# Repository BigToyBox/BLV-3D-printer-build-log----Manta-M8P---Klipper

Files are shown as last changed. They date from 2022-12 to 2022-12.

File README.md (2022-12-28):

# "The WASP" - a BLV CoreXY printer build with MantaM8P and Klipper

#### This is a log of my BLV mgn cube 3d Printer. I built the the FYSETC kit with Bluerolls metal kit recommended by Ben Levi. 

This guide combines the build guides and metal kit animations from Ben Levi, FYSETC factory videos, and David Husolo's guide on [ifixit](https://www.ifixit.com/Device/BLV_MGN_Cube) to provide a build flow that I followed to assemble my BLV printer. It's not the ONLY way to accomplish the build, it's simply a log of how I worked my way thru the build. 

### Modifications include:
- BTT Manta M8P with their CB1 pi clone
- Klipper firmware
- BIQU H2 direct drive extruder mounted with the BIQU hermit crab back plate
- Induction probe for z sensing (I run the same probe on teh Manta, an Octopus and a SKR2)
- My own neopixel code controlled directly by the MantaM8P (no daughter board required)
- Microsoft camera 
- Noctua quiet power supply fan per David's guide on ifixit
- Magnetic print bed with spring steel PEI build plate
- Left and right LED light buttons (shutting off the side oppsite the camera improves video quality 
- Tool tray for tweazers and cutters
- Dual filament spool holders





## My build includes the following mods:

3. Neopixels controlled by the Manta board

## STL files
1. Bigtreetech H2 extruder/hermit crab mount adapted to the metal kit (ADXL345 mounting holes included)
2. Adapter mount plate from the Duet mounting holes to the Manta M8P board with triple fans
3. TPU mounting feet
4. Redesigned LED light strip diffusers
5. Redesigned LED neopixel diffusers
6. 

## Manta M8P-CB1 firmware
** Firmware available on request

## Configuration Checks

From the Voron website:
Stepper motor direction setup (voron site)

## Step 1 - Endstop tests
* Test each endstop by using the "Endstop" tab within the "Machine" page
* Adjust logic as needed by doing research online and/or with your board
    For the Manta M8P ..............TBD

## Step 2 - Motor tests
* Be sure to be ready to manually trip the endstop(s) with your finger if the motor(s) are moving in the wrong direction

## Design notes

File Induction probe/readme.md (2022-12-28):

# Induction probe installation

## Two for $11.99

induction probe

Installing an induction probe is not complicated compared to the BL Touch. The reason so many people struggle and fail is because they think the probe is supposed to be powered with 5 volts to provide the required 5 volt output. It needs to be powered at the highest DC voltage you have available on your board. It works with 12 volts but 24 volts is best. I simply use a spare fan port and set the pin to the highest available. 

#### Sample code:

[probe]
pin: !PF6 # set for the pin of YOUR board!

x_offset: 35 # this is the offset for my probe mount to a H2 extruder

y_offset: -28 # this is the offset for my probe mount to a H2 extruder

speed: 20

samples: 2

samples_result: median

#### * Go to the klipper endstop test menu and test the logic using a metal object (I use a metal ruler)
#### ** When testing the probe, have a metal ruler handy. Manually run your gantry up far from the bed try a z home and immediately use your metal ruler to test the probe. If it doesn't stop the gantry, you have time to hit the panic button!

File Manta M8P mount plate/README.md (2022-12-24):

## Manta M8P Mount Plate
I created a mounting plate to mount my Manta M8P in the existing Duet mounting holes. I used the three extra fans that came with the Fysetc kit and put them to good use cooling the stepper drivers.

1. Print in PLA or PETG

2. Connect to "Motor fan" port as shown in the picture. There is no configuration necessary. This fan port runs when the board is powered up. 



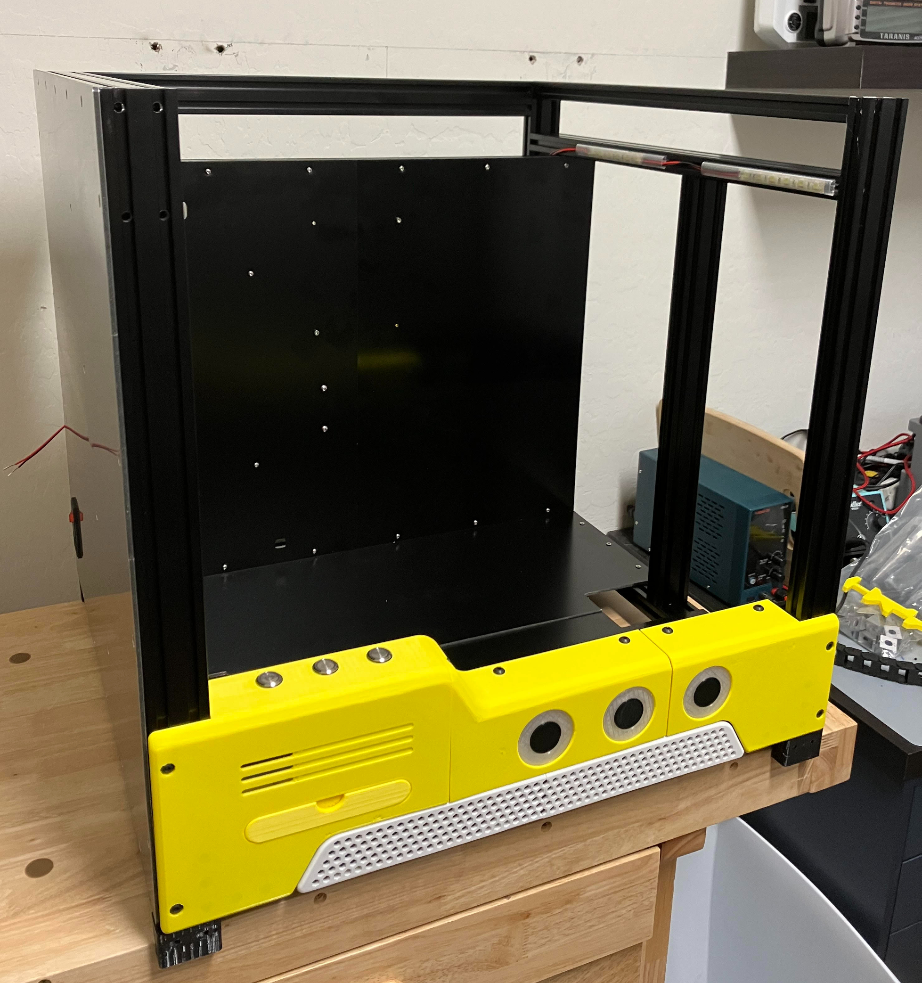
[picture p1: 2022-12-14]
blv2.jpg

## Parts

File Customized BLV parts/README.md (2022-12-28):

# Customized BLV parts

To better segment the neopixel light rings, I modified the lenses and backplates. Choose an insert, drop in the neopixel ring and attach the back plate to sandwich it all together. There are small alignment marks to help you line up the leds square in the lens. 

## Custom neopixel parts and code

https://user-images.githubusercontent.com/120577343/209478114-9a8a7863-4ae0-4498-9a60-9b79ae05963c.MOV

https://user-images.githubusercontent.com/120577343/209478135-262ede98-7630-4743-8846-90822e58087a.MOV 

https://user-images.githubusercontent.com/120577343/209478141-fe76ba48-79a5-4c61-93c1-53a307766526.MOV

lens inserts

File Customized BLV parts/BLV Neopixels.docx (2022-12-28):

Neopixel basic colors:

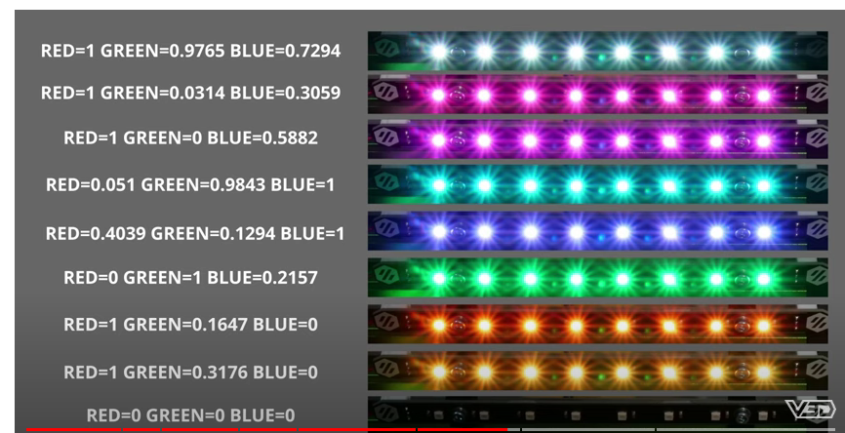
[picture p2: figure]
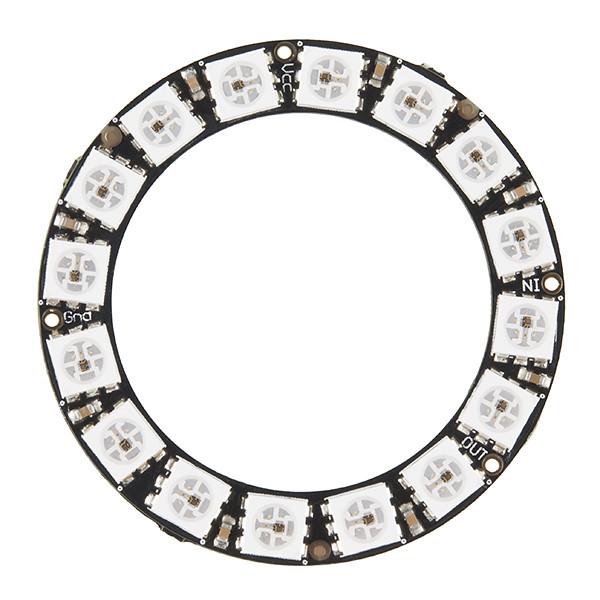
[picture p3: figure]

LEFT CENTER RIGHT

SCHEME:

Power up Manta M8P wiring

Green left ring lower and upper IN VCC GND PIN# .

Green first led center ring Left/Center Pink Red Brown PC6

Light red right ring Right Yellow Green Blue PA9

Bed heat - lower left ring

Yellow progress sequence during warm up

Red when at temp

Extruder heat - upper left ring

Yellow progress sequence during warm up

Red when at temp

Print progress - center ring

Blue progress sequence

Failure - right ring

Red flashing for errors

Red while extruder and bed are above 50C warning against a power shutdown

1. Install:

cd ~

git clone https://github.com/julianschill/klipper-led_effect.git

cd klipper-led_effect

./install-led_effect.sh

2. Add to printer.cfg

[include led_configuration.cfg]

[neopixel left]

pin: PC6

chain_count: 32

initial_red: 0

initial_green: 0

initial_blue: 0

[neopixel right]

pin: PA9

chain_count: 16

initial_red: 0

initial_green: 0.2

initial_blue: 0.2

3. Create led_configuration.cfg:

[led_effect panel_idle]

autostart: true

frame_rate: 24

leds:

neopixel:left (4,5,12,13)

layers:

breathing 10 0 top (.1,.2,0)

[led_effect power_idle]

autostart: true

frame_rate: 24

leds:

neopixel:right (1,3,5,7,9,11,13,15)

layers:

breathing 10 0 top (0.2,0.05,0.0)

[led_effect progress_idle]

autostart: true

frame_rate: 24

leds:

neopixel:left (17,32)

layers:

breathing 10 0 top (0.01,.01,.03)

[led_effect bed_effects]

leds:

neopixel:left (1-8)

neopixel:right (2,4,6,8,10,12,14,16)

autostart: true

frame_rate: 24

heater: heater_bed

layers:

heater 50 0 add (.1,0,0)

[led_effect extruder]

leds:

neopixel:left (9-16)

neopixel:right (2,4,6,8,10,12,14,16)

autostart: true

frame_rate: 24

heater: extruder

layers:

heater 50 0 add (.1,0,0)

[led_effect progress_bar]

leds:

neopixel:left (18-32)

autostart: true

frame_rate: 24

layers:

progress -1 0 add ( 0, 0, .1),( 0, 0.1, 0.6)

[led_effect critical_error]

leds:

neopixel:right (2,4,6,8,10,12,14,16)

layers:

strobe 1 1.5 add (1.0, 1.0, 1.0)

breathing 2 0 difference (0.95, 0.0, 0.0)

autostart: false

frame_rate: 24

run_on_error: true

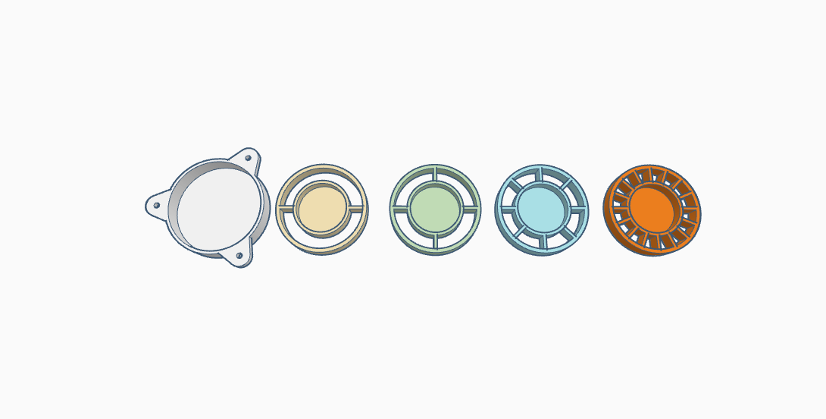
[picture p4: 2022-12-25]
Customized BLV parts/lens inserts.png

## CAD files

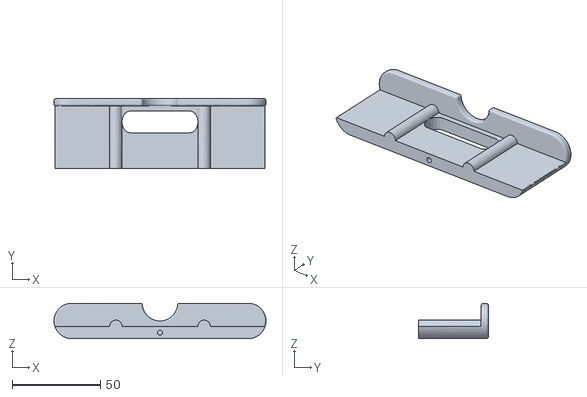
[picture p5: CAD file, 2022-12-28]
Customized BLV parts/Front pull out tool tray.stl
120.0 x 39.4 x 20.0

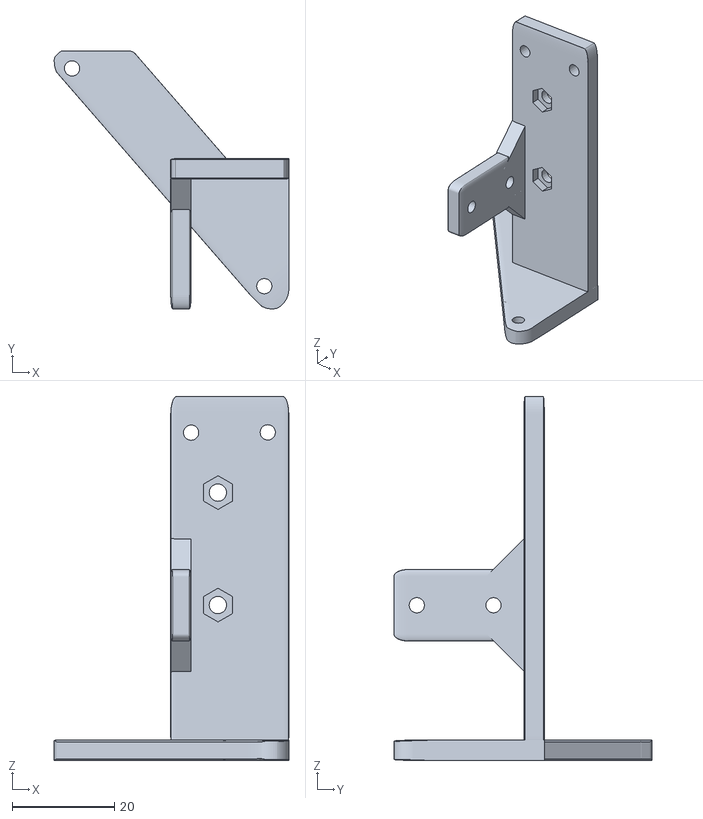
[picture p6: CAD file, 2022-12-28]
H2 - Hermit crab setup/H2 upper mount.stl
45.9 x 50.5 x 71.2

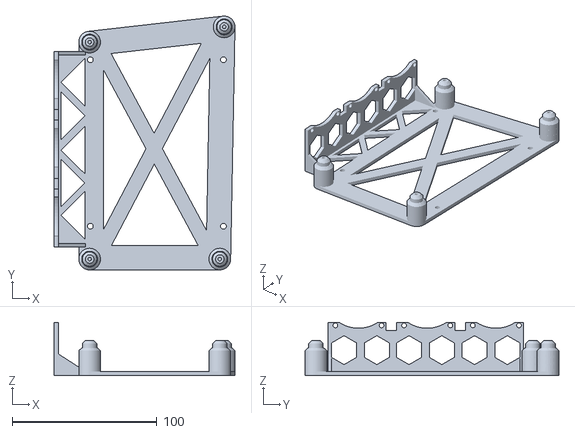
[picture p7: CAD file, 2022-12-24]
Manta M8P mount plate/Manta M8P mount.stl
125.1 x 175.5 x 36.9

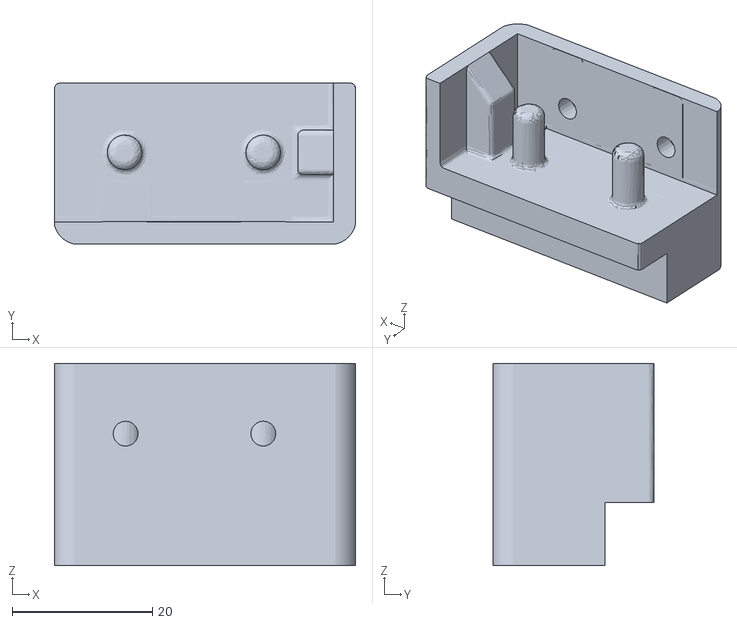
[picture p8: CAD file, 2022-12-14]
Mounting feet/BLV locking foot.stl
43.0 x 23.0 x 28.9

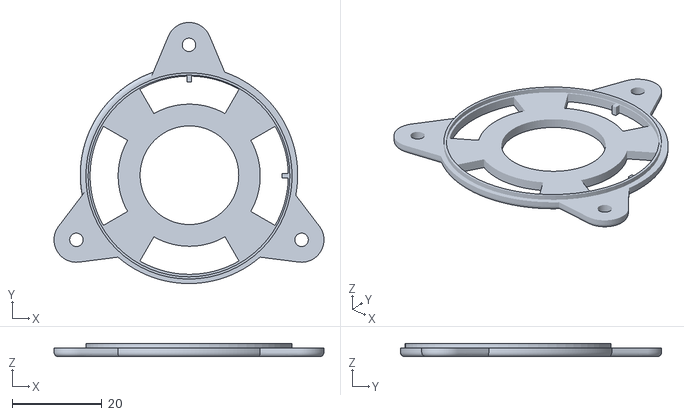
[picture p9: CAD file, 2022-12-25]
Customized BLV parts/neopixel lens back plate.stl
60.2 x 58.2 x 3.00

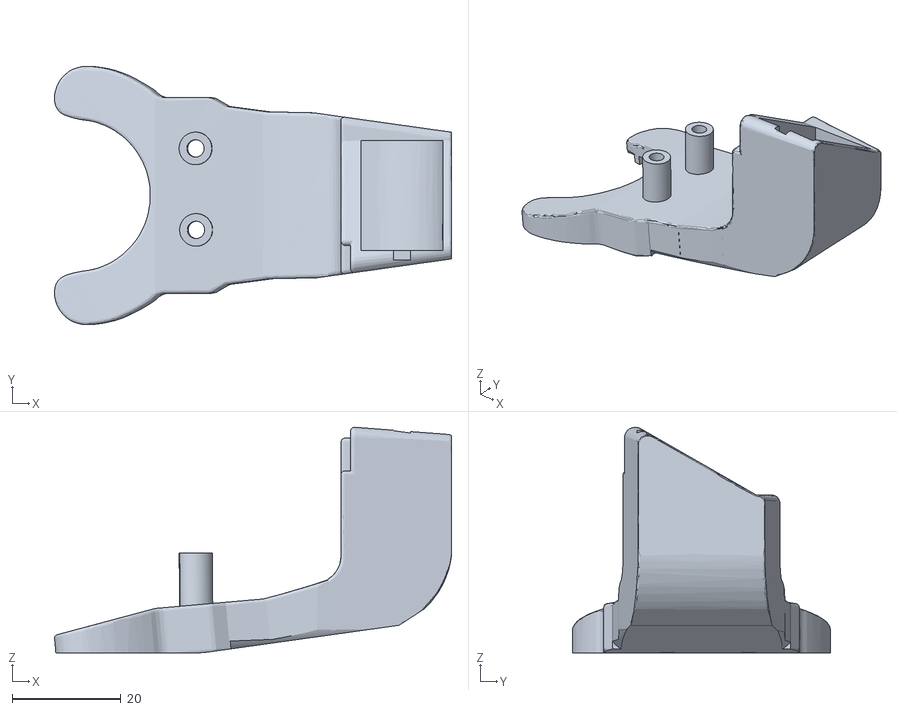
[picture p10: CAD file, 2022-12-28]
H2 - Hermit crab setup/H2 extruder fan duct.stl
73.1 x 47.6 x 41.5

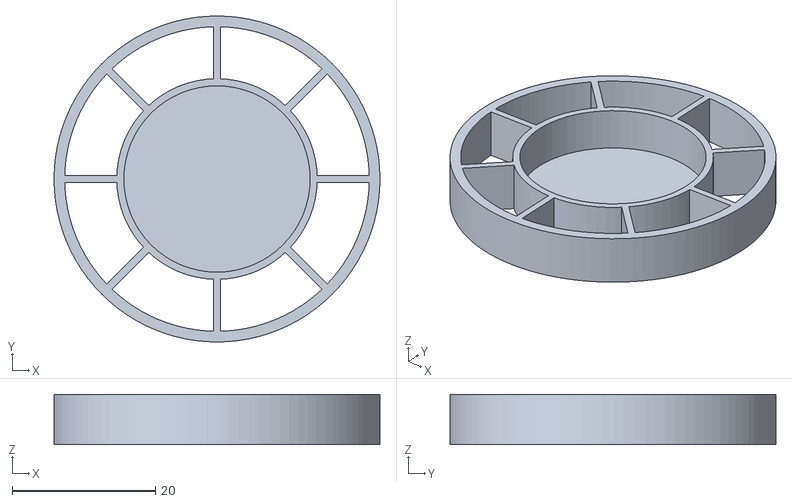
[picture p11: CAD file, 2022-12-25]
Customized BLV parts/neopixel 8 segment face.stl
45.5 x 45.5 x 7.00

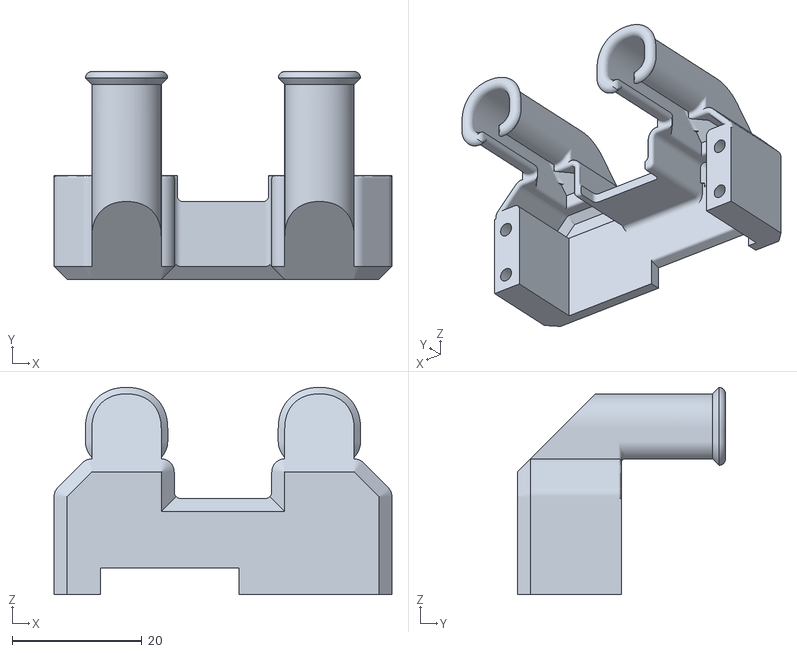
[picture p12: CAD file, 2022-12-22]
H2 - Hermit crab setup/Hermit Crab Cap.stl
52.0 x 32.0 x 31.9

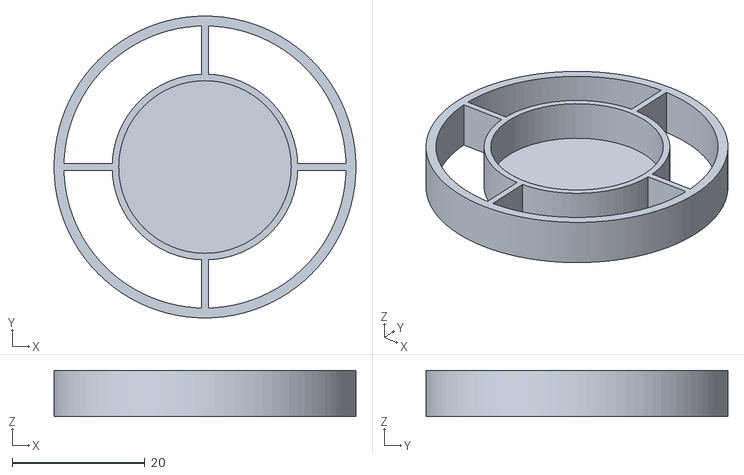
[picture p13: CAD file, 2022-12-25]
Customized BLV parts/neopixel 4 segment face.stl
45.5 x 45.5 x 7.00

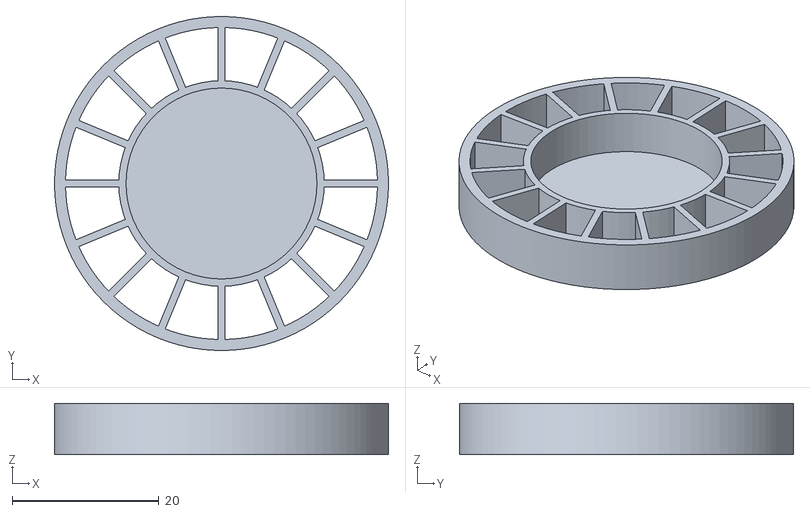
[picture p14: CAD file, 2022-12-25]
Customized BLV parts/neopixel 16 segment face.stl
45.5 x 45.5 x 7.00

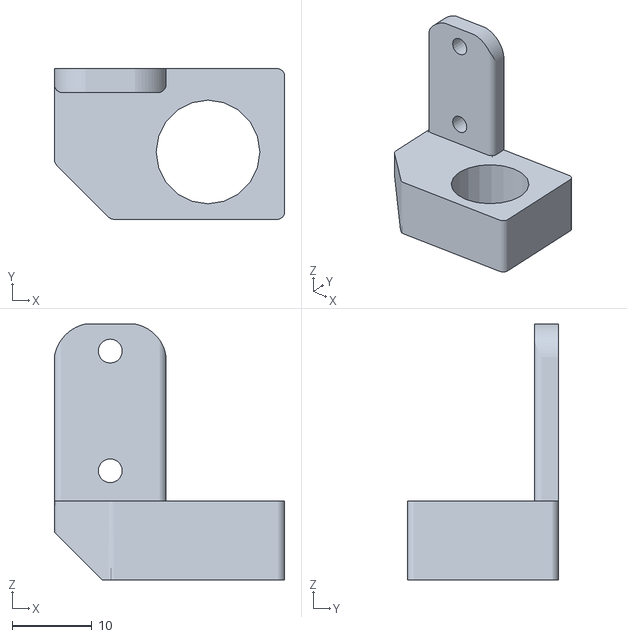
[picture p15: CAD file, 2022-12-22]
H2 - Hermit crab setup/H2 probe mount.stl
28.9 x 18.9 x 32.1

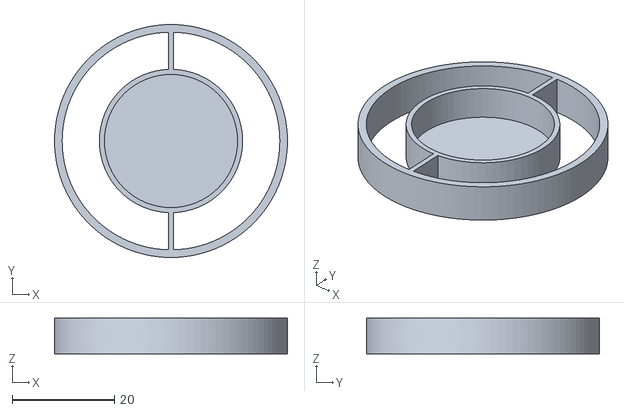
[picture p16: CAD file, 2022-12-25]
Customized BLV parts/neopixel 2 segment face.stl
45.5 x 45.5 x 7.00

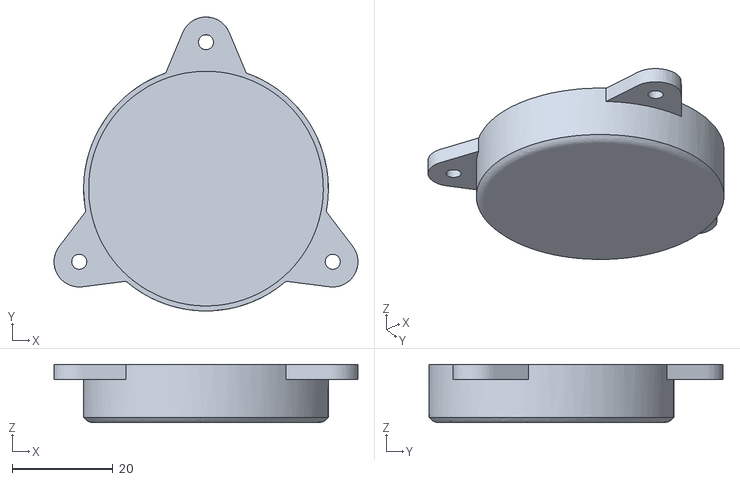
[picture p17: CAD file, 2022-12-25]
Customized BLV parts/neopixel smooth lens.stl
60.2 x 58.2 x 11.5

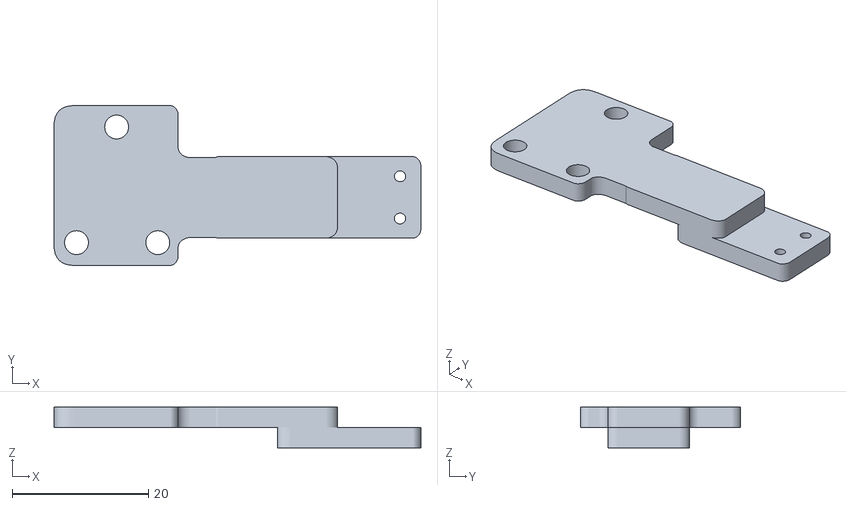
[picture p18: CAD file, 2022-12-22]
Customized BLV parts/X endstop long switch mount.stl
54.0 x 23.5 x 6.00

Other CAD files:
Customized BLV parts/Microsoft_HD_3000_2020_Rail_Mount.stl
Customized BLV parts/LED diffuser set.stl
H2 - Hermit crab setup/H2 to carriage spacer nut plate.stl

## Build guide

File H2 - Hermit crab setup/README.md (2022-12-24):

## Biqu H2 extruder and Biqu Hermit crab Assembly

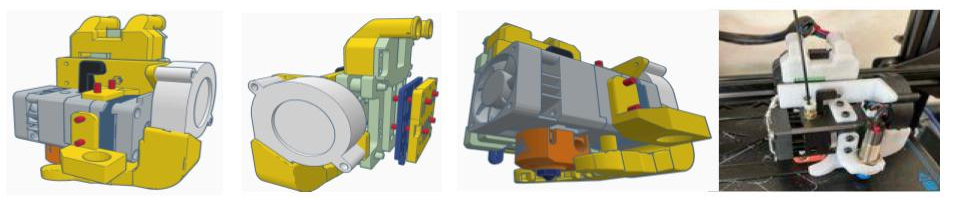
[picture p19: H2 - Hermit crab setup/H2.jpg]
H2 Hermit Crab BLV metal kit mount


## Step 1 - Print the parts:
Print the parts in PETG
 * The upper H2 mount prints best vertical as shown with a support
 * The fan duct prints flat without supports

## Step 2 - Hermit Crab back plate:
1. Insert four M3 nuts into the nut plate spacer
2. Assemble the front metal plate, the spacer and the metal top plate together OFF the gantry using two bolts provided with the metal kit
 #### You MUST USE the exact length of bolts for the top mount locations! A longer bolt will drive into the upper metal part and NOT tighten the hermit crab  plate down properly!
3. Carefully drill out the the front metal plate using the spacer as your drill guide

  

6. Finish assembly of the gantry extruder carrier
7. Bolt the back plate of the hermit crab to the face of the extruder mount using the bolts provided by BIQU
8. Connect your wires and install the wire cap

 

### Step 3 - H2 extruder assembly:
1. Remove the wiring plate from the hermit crab plate. Install the H2 with one bolt in the lower left of the plate to the lower left hole in the back of the H2 extruder. Leave it snug to allow for alignment later. 
2. Install the printed top mount using two bolts and nuts to attach it to the plate and two more bolts to attach it to the H2 extruder. Tighten the printed mount to the top of the H2 extruder first, then snug up the bolts to the plate. The printed mount si designed to provide a top "fence" for the H2 to rest against so align the H2, the printed upper mount, and the hermit crab plate so the H2 sits flush against the mount and everything is square to teh back plate. Tighten all 5 bolts. 
3. Attach the fan to the side of the mount
4. Attach the fan duct to the bottom of the H2 extruder
5. Attach the probe mount to the front of the extruder (substitute a BL touch mount if that is your preference)
6. Route all wires

  
 

## Enjoy the ease of having swappable extruders!
#### In my workflow, I have three of these assemblies, one for each printer and a fourth spare H2 assembly ready to go should one of my other H2's fail. 

#### * Note: It is impossible to have every probe set exactly the same distance from teh nozzle tip. When you swap extruders, you have to do a quick z offest "tune" using the piece of paper method. However, due to the precise design of the hermit crab system, you do NOT have to recalibrate the z offset id you remove the extruder and pop it back on the same printer. I have done it dozens of times.

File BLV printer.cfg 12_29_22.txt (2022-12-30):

# USE AT YOUR OWN RISK!
# This file contains common pin mappings for the BIGTREETECH Manta M8P
# To use this config, the firmware should be compiled for the
# STM32G0B1 with a "8KiB bootloader" and USB communication.
# See docs/Config_Reference.md for a description of parameters.

[include mainsail.cfg]
[include led_configuration.cfg]
[include timelapse.cfg]

[temperature_sensor MCU]
sensor_type: temperature_mcu

[temperature_sensor SoC]
sensor_type: temperature_host

[mcu]
serial: /dev/serial/by-id/usb-Klipper_stm32g0b1xx_m8p-if00

[printer]
kinematics: corexy
max_velocity: 300  
max_accel: 5000           #suggested X= "mzv" max accel <12400, Y= "mzv" max accel <5600
max_accel_to_decel: 5000
max_z_velocity: 15                         #Max 15 for 12V TMC Drivers, can increase for 24V
max_z_accel: 350
square_corner_velocity: 5.0

#####################################################################
#         X/Y Stepper Settings
#####################################################################

## X Stepper on Motor1(B Motor on LEFT)
[stepper_x]
step_pin: PE2
dir_pin: !PB4
enable_pin: !PC11
microsteps: 16
rotation_distance: 32
full_steps_per_rotation: 400    # set t0 200 for 1.8 motor or 400 for 0.9 motor
endstop_pin: PF3
position_endstop: 0
position_min: 0
position_max: 300
homing_speed: 40

## Y Stepper on Motor2 (A Motor on RIGHT)
[stepper_y]
step_pin: PF12
dir_pin: PF11
enable_pin: !PB3
microsteps: 16
rotation_distance: 32
full_steps_per_rotation: 400    # set to 200 for 1.8 motor or 400 for 0.9 motor
endstop_pin: ^PF4
position_endstop: 300
position_min: 0
position_max: 300
homing_speed: 40

#####################################################################
#         Z Stepper Settings
#####################################################################

## Z Stepper - Right side Motor3, Socket 3A (socket 3B is for a second Z motor without z tilt)
[stepper_z]
step_pin: PD7
dir_pin: !PD6
enable_pin: !PF10
microsteps: 16
rotation_distance: 8
endstop_pin: probe:z_virtual_endstop
position_max: 335
position_min: -5.0
homing_speed: 10
homing_retract_dist: 0

## Z1 Stepper - Left side Motor4 (use with Z tilt feature)
[stepper_z1]
step_pin: PD3
dir_pin: !PD2
enable_pin: !PD5
microsteps: 16
rotation_distance: 8

[z_tilt]
z_positions: 0,150 
    200,150 
points: 0,150 
    250,150
retries: 7
retry_tolerance: 0.02 
speed: 50

[safe_z_home]
home_xy_position: 150,150
speed: 50
z_hop: 5
z_hop_speed: 5

[extruder]  # Motor 5
step_pin: PC9
dir_pin: !PC8
enable_pin: !PD1
microsteps: 16
rotation_distance: 3.4334
nozzle_diameter: 0.4
filament_diameter: 1.75
heater_pin: PE3 # HE0
sensor_pin: PA1 # T0
sensor_type: EPCOS 100K B57560G104F
min_temp: 0
max_temp: 250
pressure_advance: 0.04
#control: pid
#pid_kp: 22
#pid_ki: 1.1
#pid_kd: 114

#[filament_switch_sensor material_0]
#switch_pin: PC1

# Motor6
#[extruder1]
#step_pin: PA10
#dir_pin: PD15
#enable_pin: !PA15
#heater_pin: PB5 # HE1
#sensor_pin: PA2 # T1
#...

#[filament_switch_sensor material_1]
#switch_pin: PC2

# Motor7
#[extruder2]
#step_pin: PD12
#dir_pin: PD11
#enable_pin: !PD14
#heater_pin: PB6 # HE2
#sensor_pin: PA3 # T2
#...

# Motor8
#[extruder3]
#step_pin: PD10
#dir_pin: PD8
#enable_pin: !PD9
#heater_pin: PE1 # HE3
#sensor_pin: PA4 # T3
#...

[heater_bed]
heater_pin: PB7
sensor_pin: PA0 # TB
sensor_type: ATC Semitec 104GT-2
#control: watermark
min_temp: 0
max_temp: 130
max_power: 0.8

#####################################################################
#         Fan Control
#####################################################################

[fan]
##        Print Cooling Fan - CNC_FAN0
pin: PE6
kick_start_time: 0.5
##        Depending on your fan, you may need to increase this value
##        if your fan will not start. Can change cycle_time (increase)
##        if your fan is not able to slow down effectively
off_below: 0.10

[heater_fan hotend_fan]
##        Hotend Fan - CNC_FAN1
pin: PE0
max_power: 1.0
kick_start_time: 0.5
heater: extruder
heater_temp: 50.0
##        If you are experiencing back flow, you can reduce fan_speed
#fan_speed: 1.0

#[heater_fan controller_fan]
##        Controller fan - CNC_FAN2
#pin: PC12
#kick_start_time: 0.5
#heater: heater_bed
#heater_temp: 45.0

#[heater_fan fan3]
#pin: PE5

#[heater_fan fan4]
#pin: PE4
#tachometer_pin: PC13

#[heater_fan fan5]
#pin: PB8
#tachometer_pin: PC14

#[heater_fan fan6]
#pin: PB9
#tachometer_pin: PC15

######################################################
# INPUT SHAPING
######################################################

#[mcu pico]
#serial: /dev/serial/by-id/usb-Klipper_rp2040_E66118C4E31E8A2A-if00

#[adxl345]
#spi_bus: spi0a
#cs_pin: pico:gpio1

#[resonance_tester]
#accel_chip: adxl345
#probe_points:
    #150,150,20 # an example
#max_smoothing: 0.1

########################################
# TMC2209 configuration
########################################

[tmc2209 stepper_x]
uart_pin: PC10
run_current: 0.800
#hold_current: 0.7
#stealthchop_threshold: 999999

[tmc2209 stepper_y]
uart_pin: PF13
run_current: 0.800
#hold_current: 0.7
#stealthchop_threshold: 999999

[tmc2209 stepper_z]
uart_pin: PF9
##diag_pin: PF5
run_current: 0.800
#hold_current: 0.5
#stealthchop_threshold: 999999

[tmc2209 stepper_z1]
uart_pin: PD4
##diag_pin: PC0
run_current: 0.800
#hold_current: 0.5
#stealthchop_threshold: 999999

[tmc2209 extruder]
uart_pin: PD0
run_current: 0.800
#Hold_current: 0.5

#[tmc2209 extruder1]
#uart_pin: PF8
#run_current: 0.800
#stealthchop_threshold: 999999

#[tmc2209 extruder2]
#uart_pin: PD13
#run_current: 0.800
#stealthchop_threshold: 999999

#[tmc2209 extruder3]
#uart_pin: PC7
#run_current: 0.800
#stealthchop_threshold: 999999

[board_pins]
aliases:
    # EXP1 header
    EXP1_1=PE9, EXP1_2=PE10,
    EXP1_3=PE11, EXP1_4=PE12,
    EXP1_5=PE13, EXP1_6=PE14,    # Slot in the socket on this side
    EXP1_7=PE15, EXP1_8=PB10,
    EXP1_9=<GND>, EXP1_10=<5V>,

    # EXP2 header
    EXP2_1=PB14, EXP2_2=PB13,
    EXP2_3=PF7, EXP2_4=PB12,
    EXP2_5=PE7, EXP2_6=PB11,      # Slot in the socket on this side
    EXP2_7=PE8, EXP2_8=<RST>,
    EXP2_9=<GND>, EXP2_10=PC5

#####################################################################
#         Probe
#####################################################################

[probe]
##        Inductive Probe
##        NPN and PNP proximity switch types can be set by jumper
pin: !PF6
x_offset: 35
y_offset: -28
#z_offset: 0
speed: 20
samples: 2
samples_result: median
#sample_retract_dist: 3.0
####################################################################
[bed_screws]
screw1: 50, 50
screw2: 250, 50
screw3: 250, 250
screw4: 50, 250
####################################################################

#PS Power control switch
#[output_pin ps_on_pin]
#pin: PC3

####################################################################
# Neopixel
####################################################################
[neopixel left]
pin: PC6
chain_count: 32
initial_red: 0
initial_green: 0
initial_blue: 0

[neopixel right]
pin: PA9
chain_count: 16
initial_red: 0
initial_green: 0.2
initial_blue: 0.2
#####################################################################

#*# <---------------------- SAVE_CONFIG ---------------------->
#*# DO NOT EDIT THIS BLOCK OR BELOW. The contents are auto-generated.
#*#
#*# [probe]
#*# z_offset = 2.129
#*#
#*# [extruder]
#*# control = pid
#*# pid_kp = 21.759
#*# pid_ki = 0.697
#*# pid_kd = 169.717
#*#
#*# [heater_bed]
#*# control = pid
#*# pid_kp = 68.502
#*# pid_ki = 1.075
#*# pid_kd = 1091.745
#*#
#*# [input_shaper]
#*# shaper_type_x = zv
#*# shaper_freq_x = 65.2
#*# shaper_type_y = mzv
#*# shaper_freq_y = 45.2

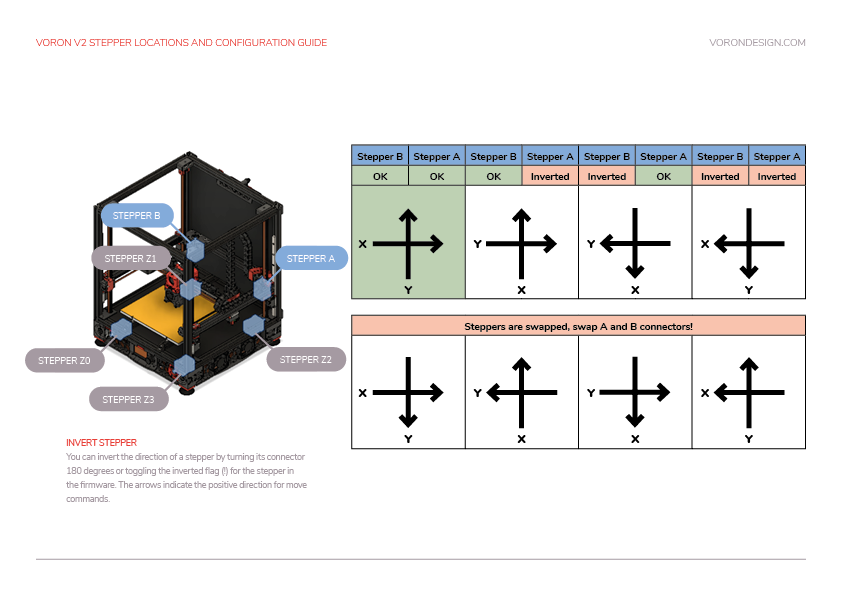
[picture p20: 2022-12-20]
Stepper motor direction setup (voron site).png

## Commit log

2022-12-20 Create H2 Extruder with hermit crab mount
2022-12-22 Rename readme.md to Probe Setup
2022-12-22 Create Duet to Manta M8P mount
2022-12-22 Rename readme.md to Assembly instructions.md
2022-12-22 Update Assembly instructions.md
2022-12-22 Update and rename Probe Setup to Probe Setup.md
2022-12-22 Update Probe Setup.md
2022-12-24 Update and rename Duet to Manta M8P mount to Duet to Manta M8P mount.mb
2022-12-24 Update and rename Duet to Manta M8P mount.mb to Duet to Manta M8P mount.md
2022-12-24 Update Duet to Manta M8P mount.md
2022-12-24 Rename Duet to Manta M8P mount.md to Duet to Manta M8P mount read me.md
2022-12-24 Rename Duet to Manta M8P mount read me.md to README.md
2022-12-24 Rename Assembly instructions.md to README.md
2022-12-30 Update BLV printer.cfg 12_29_22.txt
